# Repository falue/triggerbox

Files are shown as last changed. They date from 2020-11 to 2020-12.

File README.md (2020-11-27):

# triggerbox

## Introduction

This system allows for triggering up to six relays in a specific, as precice-as-possible rhythm.
It is designed for **high speed photography** or **high speed cinema shootings**,
where it can release water droplets, trigger explosions, activate a solenoid or anything that can be started with **up to 30VDC**.

Each relay can be tuned to start and stop being closed, starting when a button is pushed.
As in my hardware setup, each relay can hold up to **30VDC @ 5amps** and is able to trigger any external DC powered motor, electro magnet, or the like.

There is a 320x480 TFT display necessary to display a graphical menu, and give some feedback to the user. This can be omitted if you'd like to implement serial communication controls for user input.

The accuracy of the timing has to be determined. Theoretically you can set on / off timestamps in a microsecond fashion (0.000001s), but this is heavily influenced by the programs efficiency, the relay reaction time and the microcontrollers speed itself. More important than the preciseness to your entered timestamps though is the **repeatability**. If you do not change the hardware, the system should always trigger the relays with about the same lag, leading to the same results each time.

This system can be triggered with a regular hardwired push button. You are able to extend the triggering to another system: Connect it to your camera flash system, wire to two metal connectors, or use another arduino.

Maximum delay of any trigger is 35.79mins, theoretical minimum duration 0.000001s (1 microsecond, depending on the speed of the relays used).

## Hardware

This project needs eg. an Adafruit Metro M0 Express to work properly. Its program size and the demands for speed exceeds the capabilities of an Arduino UNO or Leonardo.

## Wiring diagram

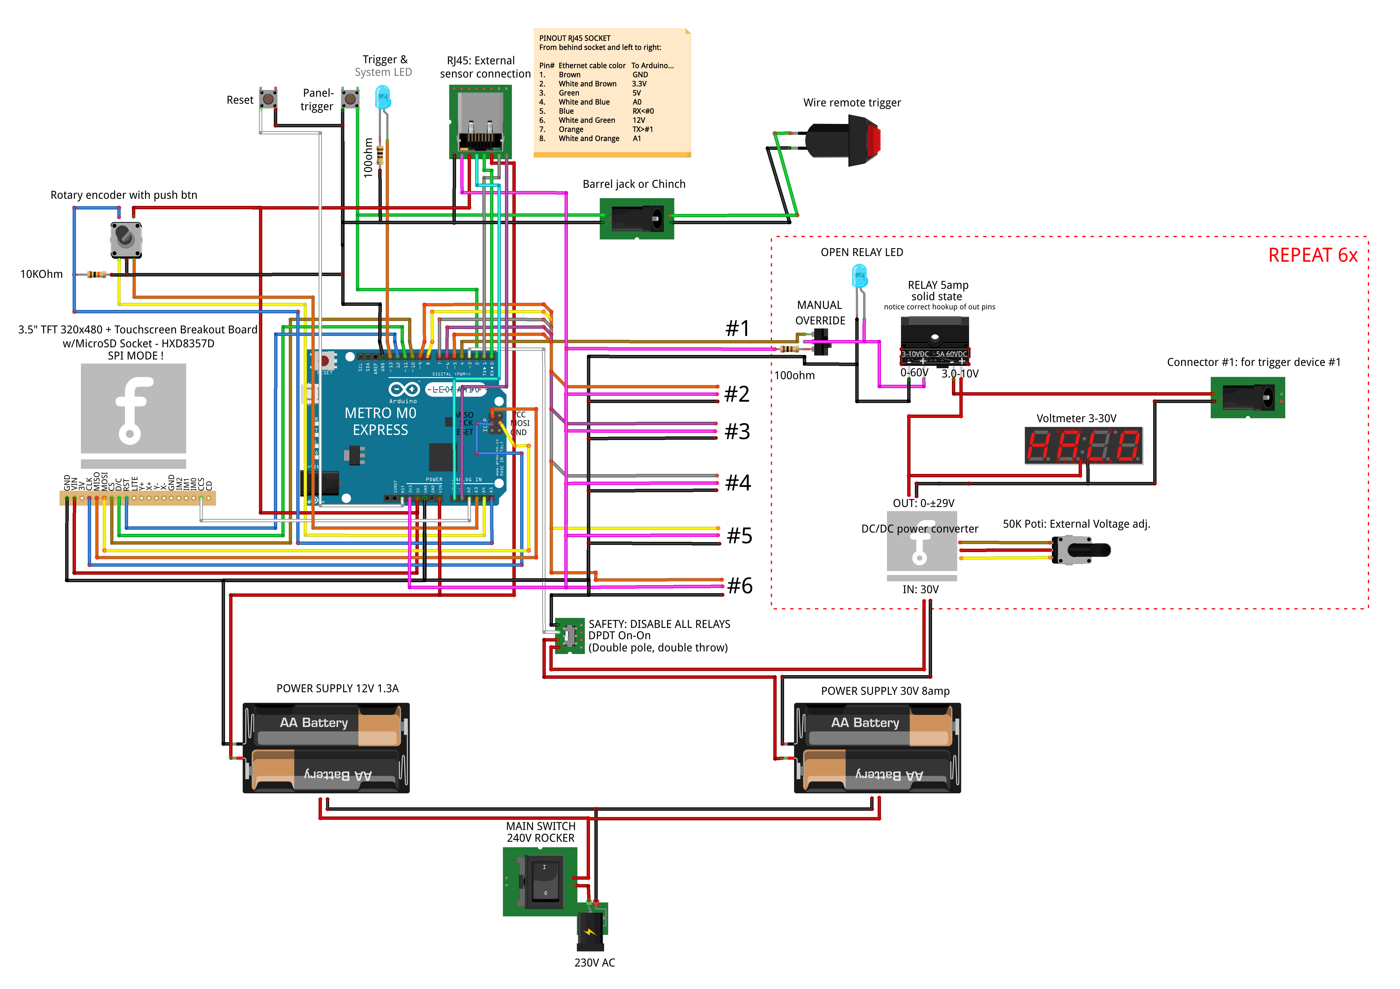
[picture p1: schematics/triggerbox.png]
wiring


### Hardware list

- Metro M0 Express - https://www.adafruit.com/product/3505
- TFT Touchscreen Breakout Board - HXD8357D - https://www.adafruit.com/product/2050
- 6pcs Solid state relays - https://www.digikey.ch/product-detail/en/sensata-crydom/CMX60D5/CC1667-ND/751911
- 30VDC power supply 8amp - https://www.components-store.com/product/MEAN-WELL/SP-240-30.html
- 5VDC power supply 5amp - https://www.components-store.com/product/MEAN-WELL/RS-25-5.html
- Generic rotary encoder
- Generic push button
- Some generic resistors
- Generic AC cold appliance socket

### Optional hardware
- 7pcs generic LEDs (display relay action)
- 6pcs DC/DC 15A Buck Adjustable 4-32V 12V to 1.2-32V 5V Converter Step Down Module DT (adjustment of relay voltage) - https://ebay.us/CVko1q
- 6pcs Generic 50KΩ potentiometer (allow for free placement of potentiometer of the Step Down Module)
- 6pcs LED Digital Voltmeter 0-100V (display chosen voltage) - https://de.aliexpress.com/item/33017235960.html?spm=a2g0s.9042311.0.0.64224c4dII9GZf

Keep an eye on the fact that your solid state relay can switch loads from ***0VDC*** to 30VDC.
Cheaper relays may only trigger loads from eg. ***14VDC*** to 30VDC, which may also work for your use case.

## Attention: Electricity

Although this setup allows for each relay to hold **5amps**, the sum of active loads in parallel **cannot be greater than 8 amps**.
The bottleneck is the 30VDC power supply with only 8amps. If you choose something beefier, you can trigger more loads @ 5amps in parallel.

Also, this system handles ***mains voltage***. No fingers where they do not belong. Its components are chosen based on a 230V AC/DC environment.

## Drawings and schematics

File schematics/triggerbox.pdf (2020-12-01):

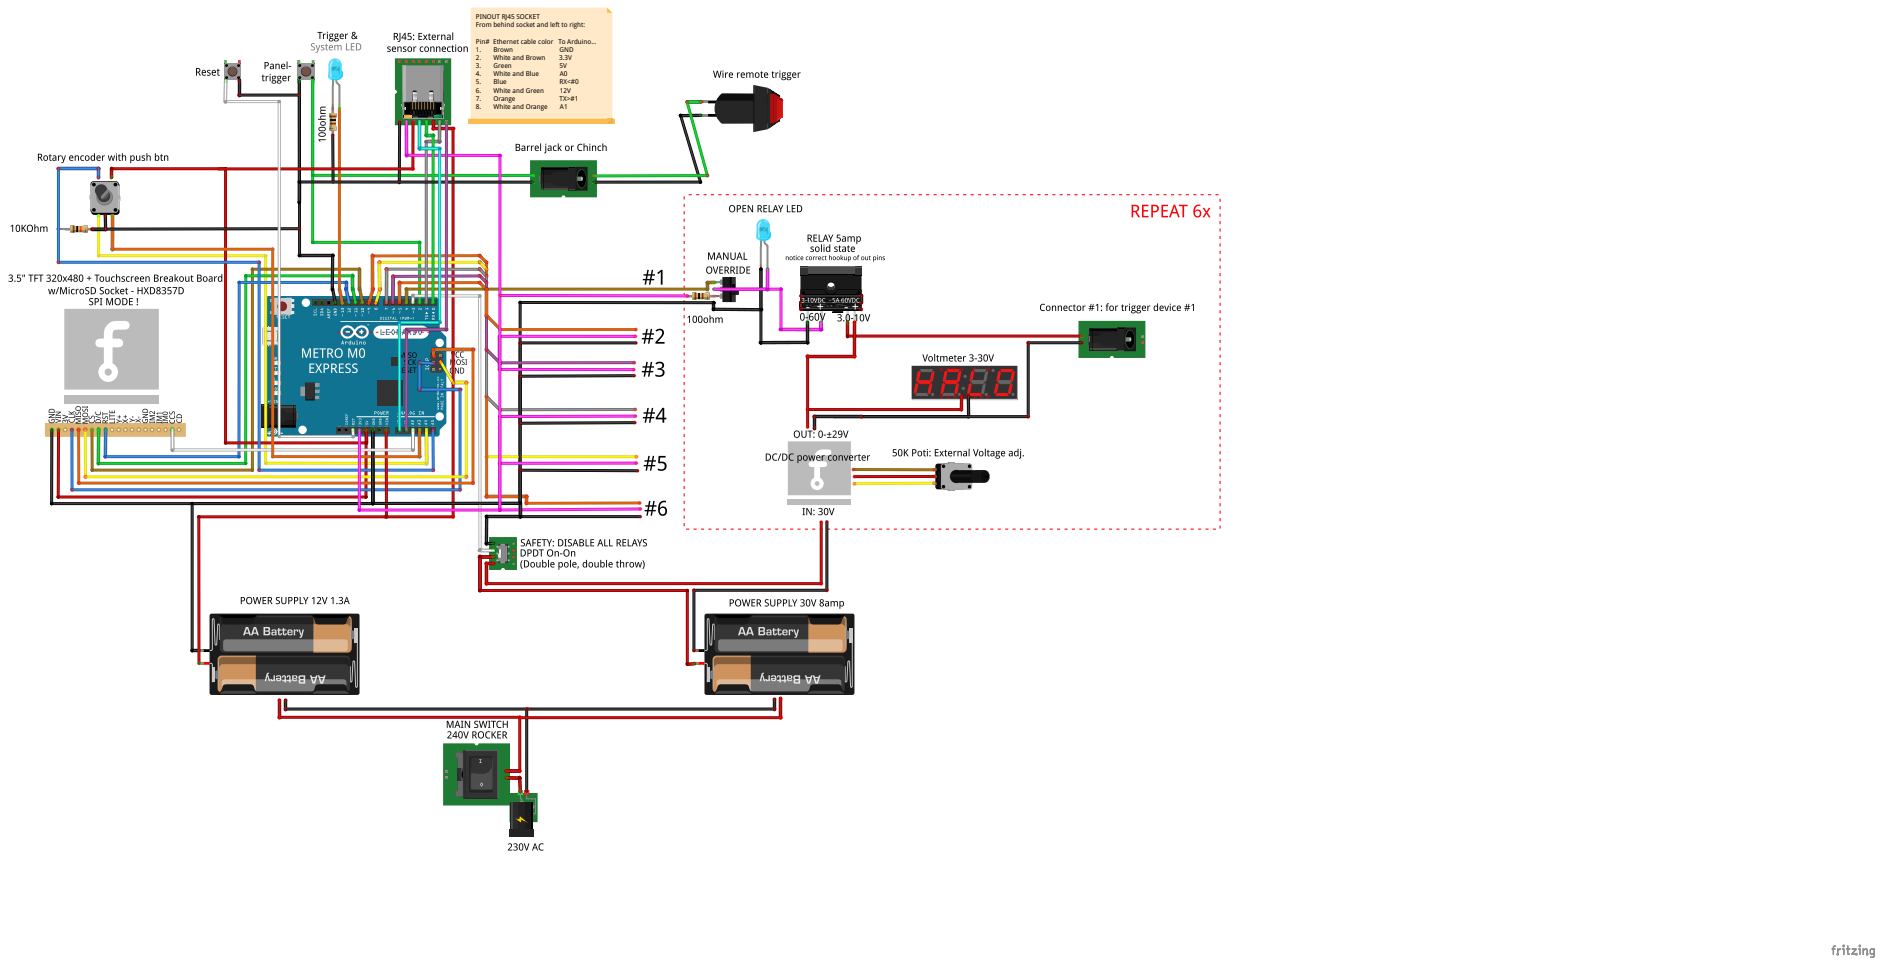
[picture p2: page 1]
Brown; GND; White and Brown; Green; White and Blue; Blue; White and Green; Orange; White and Orange

PINOUT RJ45 SOCKET
From behind socket and left to right:

Pin# Ethernet cable color To Arduino...

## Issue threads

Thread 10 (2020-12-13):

Pushing of Rotary Encoder lights up LEDs

falue, 2020-12-13:
If a relay is set to "manual override", during the push of the Rotary encoder btn, the LED lights up brigther.
Something to do with the 5V used for the push btn.
Maybe seperate the 5V GND and the 3.3V GND?

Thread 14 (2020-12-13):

Install more fuses

falue, 2020-12-13:
Maybe more fuses are needed to protect the expensive circuit? But where?
Some components are already protected by fuses, like the DC-DCconverter or the power supplies. But the relays and the TFT are not.

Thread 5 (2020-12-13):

Inverse trigger mechanics on demand

falue, 2020-12-13:
Allow any trigger relay to be set as "reverse", so that it is open on idle, but closed when triggering. Useful for eg. an electro magnet that should open for a specific moment.

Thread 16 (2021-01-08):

Make one relay trigger camera

falue, 2021-01-08:
One relay should be able to trigger the camera on a specific time.
i.e., wire bot poles of a relay to the external plug without a dimmer. replace "manual override" switch with a momentary switch to manually trigger camera.

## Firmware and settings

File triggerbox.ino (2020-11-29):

// INCLUDE LOCAL FILES -----------------------------------------------------------------------------
#include "includes.h"
#include "declarations.h"

// ACTIONS FOR INTERRUPTS --------------------------------------------------------------------------
// Push btn: Trigger
void triggerIsPushed() {
  if(millis() > lastTimeTriggered + 500) {
    #ifdef debug
      Serial.println("triggerIsPushed");
    #endif
    if(!editSettings && !safetyIsOn) {
      triggerIsActive = !triggerIsActive;
      if(!triggerIsActive) reset();
    } else {
      triggerIsActive = false;
      Serial.println("Safety first! Cannot trigger when in menu or when safety is on.");
    }
  }
  lastTimeTriggered = millis();
}

// Safety switch: two pole single throw
void safetySwitchChanged() {
  safetyIsOn = digitalRead(safetySwitchPin);
  if(safetyIsOn) {
    reset();
    drawSafetyPopUp();
    editSettings = false;  // exit menu when switch is thrown in edit mode
  } else {
    drawLayout();
  }
  // If, during rendering of TFT, switch was changed again, re-run function:
  if(digitalRead(safetySwitchPin) != safetyIsOn) safetySwitchChanged();
}

// SETUP --------------------------------------------------------------------------------------
void setup() {
  Serial.begin(115200);

  // Setup TFT
  tft.begin();
  tft.setRotation(1);
  screenWidth = tft.width();
  screenHeight = tft.height();

  // Draw Welcome screen
  splashScreen();

  delay(1500); // wait for serial monitor to catch up...
  Serial.println("TRIGGERBOX INITIALIZED");

  // Setup buttons
  pinMode(rotaryHomePin, INPUT);
  pinMode(triggerPin, INPUT_PULLUP);
  attachInterrupt(digitalPinToInterrupt(triggerPin), triggerIsPushed, RISING);
  pinMode(safetySwitchPin, INPUT_PULLUP);
  attachInterrupt(digitalPinToInterrupt(safetySwitchPin), safetySwitchChanged, CHANGE);

  // Setup rotary encoder
  rotaryEncoder.begin();

  // Set pinMode for relays
  for(int i = 0; i < numOfTriggers; i++) {
    /* Serial.print("triggers[i].pin: ");
    Serial.println(triggers[i].pin); */
    pinMode(triggers[i].pin, OUTPUT);
  }

  // TODO: Load "triggers" and settings (initDelay) from internal SPI Flash memory
  // https://learn.adafruit.com/adafruit-metro-m0-express-designed-for-circuitpython/using-spi-flash
  getDataFromMemory();

  // Initial save of settings
  calculateActions();
  printSettings();
  printActions();
  printTriggers();

  // Draw base layout
  drawLayout();

  safetyIsOn = digitalRead(safetySwitchPin);
  if(safetyIsOn) drawSafetyPopUp();
};


// LOOP ---------------------------------------------------------------------------------------
void loop() {
  editSettings = digitalRead(rotaryHomePin);
  if(editSettings && !safetyIsOn) {
    drawLock();
    drawFooter();  // redraw because buttons show up
    drawInitDelayButton();  // redraw because button is now selected
    Serial.println("---------");
    Serial.println("MENU");
    Serial.println("---------");
    Serial.println("Set initial delay..");
    delay(250); // wait for button to be released
  }

  // If rotary button is pressed and safety is not on, enter menu
  while(editSettings && !safetyIsOn) {
    menu();
    // If inside menu() "save" was selected, calculate actions
    if(!editSettings && !safetyIsOn) {
      calculateActions();
      printSettings();
      printActions();
      printTriggers();
      saveDataToMemory();
      drawLayout();
      Serial.println("Triggers and settings saved.");
    }
  }
  
  // If trigger push btn is pressed
  if(triggerIsActive) triggerAction();

  // Cut the loop() some slack
  delay(100);
};


// ACTIONS ------------------------------------------------------------------------------------
void menu() {
  // Names of menu items to display
  String menuDisplay[numOfMenuIds] = {
    F("Set initial delay.."),
    F("setRelay-00-startPoint"), F("setRelay-00-endPoint"), F("toggleRelay-00"),
    F("setRelay-01-startPoint"), F("setRelay-01-endPoint"), F("toggleRelay-01"),
    F("setRelay-02-startPoint"), F("setRelay-02-endPoint"), F("toggleRelay-02"),
    F("setRelay-03-startPoint"), F("setRelay-03-endPoint"), F("toggleRelay-03"),
    F("setRelay-04-startPoint"), F("setRelay-04-endPoint"), F("toggleRelay-04"),
    F("setRelay-05-startPoint"), F("setRelay-05-endPoint"), F("toggleRelay-05"),
    F("Set all to default"),
    F("Save and exit")
  };

  String selectedMenu = menuIds[menuSelector];
  String selectedMenuDisplay = menuDisplay[menuSelector];

  rotaryDirection = readRotaryEncoder(false);
  if(rotaryDirection != 0) {
    menuSelector += rotaryDirection;
    if(menuSelector > numOfMenuIds-1) menuSelector = 0;
    if(menuSelector < 0) menuSelector = numOfMenuIds-1;
    // menu level
    selectedMenu = menuIds[menuSelector];
    selectedMenuDisplay = menuDisplay[menuSelector];

    drawFooterButtons();  // redraw buttons to select or deselect
    drawInitDelayButton();  // redraw buttons to select or deselect

    // highlight relay parts
    if(selectedMenu.startsWith("setRelay") || selectedMenu.startsWith("toggleRelay")) {
      if(selectedMenu.startsWith("setRelay")) {
        relayIndex = selectedMenu.substring(9, 11).toInt();  // i know...
      } else {
        relayIndex = selectedMenu.substring(12, 14).toInt();  // i know...
      }
      if(relayIndex - 1 >= 0) drawTrigger(relayIndex-1);  // clear previous highlight
      drawTrigger(relayIndex);  // Draw to display
      if(relayIndex + 1 < numOfTriggers) drawTrigger(relayIndex+1);  // clear next highlight
      #ifdef debug
        Serial.println(getRelayMenuItem(relayIndex, selectedMenuDisplay));  
      #endif
    } else {
      #ifdef debug
        Serial.println(selectedMenuDisplay);
      #endif
    }

    if(selectedMenu == "initDelay") {  // redraw selection of trigger
      drawTrigger(0);
    }
    if(selectedMenu == "reset") {  // redraw selection of trigger
      drawTrigger(numOfTriggers-1);
    }
  }

  // Edit initDelay
  if(digitalRead(rotaryHomePin) && selectedMenu == "initDelay") {
    drawPopUp("Set initial delay");
    drawPopUpContent(timestampToFloatString(initDelay, "s", false), "");
    delay(250);  // wait for button to be depressed
    Serial.print("Edit initDelay:\t");
    Serial.println(initDelay);
    initDelay = setValueWithRotaryEncoder(initDelay, 0, 0, 1000, true);  // Edit [0.000]0000
    initDelay = setValueWithRotaryEncoder(initDelay, 0, 0, 1, true);  // Edit 0.000[0000]
    Serial.print("Saved initDelay:\t");
    Serial.print(initDelay);
    Serial.println("μs ("+String(initDelay / 1000000.0)+"..s)");
    drawLayout();
    delay(250);  // wait for btn release
  }

  // Edit start & end timestamps of relays
  if(digitalRead(rotaryHomePin) && selectedMenu.startsWith("setRelay")) {
    String relayTimepointToEdit = selectedMenu.substring(12);
    delay(250);  // wait for button to be depressed
    long lastTimeMoved = millis();

    if(relayTimepointToEdit == "startPoint") {
      drawPopUp("Set startpoint #" + String(relayIndex+1));
      drawPopUpContent(timestampToFloatString(triggers[relayIndex].startPoint, "s", false), "");
      Serial.println("Edit start point:");
      long initialGap = triggers[relayIndex].endPoint - triggers[relayIndex].startPoint;
      triggers[relayIndex].startPoint  = setValueWithRotaryEncoder(triggers[relayIndex].startPoint, 0, 2147483646-initialGap, 1000, true);  // Edit [0.000]0000
      triggers[relayIndex].startPoint  = setValueWithRotaryEncoder(triggers[relayIndex].startPoint, 0, 2147483646-initialGap, 1, true);  // Edit 0.000[0000]
      
      // re-set endpoint
      triggers[relayIndex].endPoint = triggers[relayIndex].startPoint + initialGap;
      Serial.print("Saved startPoint");
      Serial.print(triggers[relayIndex].startPoint);
      Serial.println("μs ("+String(triggers[relayIndex].startPoint / 1000000.0)+"..s)");

    } else {
      drawPopUp("Set duration #" + String(relayIndex+1));
      drawPopUpContent(timestampToFloatString(triggers[relayIndex].endPoint - triggers[relayIndex].startPoint, "s", false), "");
      Serial.println("Edit end point:");
      long delay = triggers[relayIndex].endPoint - triggers[relayIndex].startPoint;
      delay  = setValueWithRotaryEncoder(delay, 1, 0, 1000, true);  // Edit [0.000]0000
      delay  = setValueWithRotaryEncoder(delay, 1, 0, 1, true);  // Edit 0.000[0000]
      triggers[relayIndex].endPoint = triggers[relayIndex].startPoint + delay;
      Serial.print("Saved endPoint ");
      Serial.print(triggers[relayIndex].endPoint);
      Serial.println("μs ("+String(triggers[relayIndex].endPoint / 1000000.0)+"..s)");
    }
    drawLayout();
    delay(250);  // wait for btn release
  }

  if(digitalRead(rotaryHomePin) && selectedMenu.startsWith("toggleRelay")) {
    Serial.print("Edit active nr. ");
    Serial.print("di/enable ");
    Serial.println(relayIndex);
    triggers[relayIndex].active = !triggers[relayIndex].active;
    delay(250);  // wait for btn release
    editSettings = false;
  }

  // Reset to default
  if(digitalRead(rotaryHomePin) && selectedMenu == "reset") {
    initDelay = 0;
    triggers[0] = {4, 0, 1000000, true};
	  triggers[1] = {5, 1000000, 2000000, true};
	  triggers[2] = {6, 2000000, 3000000, true};
	  triggers[3] = {7, 3000000, 3500000, true};
	  triggers[4] = {8, 4000000, 4500000, true};
	  triggers[5] = {9, 5000000, 5600000, true};
    delay(250);  // wait for btn release
    editSettings = false;
  }

  // Exit menu
  if(digitalRead(rotaryHomePin) && (selectedMenu == "exit")) {
    Serial.println("Exit menu.");
    delay(250);  // wait for btn release
    editSettings = false;
  }
}

long setValueWithRotaryEncoder(long value, long min, long max, int multiplicator, boolean inertia) {
  long lastTimeMoved = millis();
  max = max == 0 ? 2147483646 : max;  // if 0 is max, use highest possible long
  while(!digitalRead(rotaryHomePin)) {
    long reading = readRotaryEncoder(inertia)*multiplicator;
    if(reading != 0) {
      value += reading;
      //value = value >= 0 ? value : 0;
      value = value >= min ? value : min;
      value = value <= max ? value : max;  // max size of type long (35.79min)
      /* Serial.print(value);
      Serial.println("μs ("+String(value / 1000000.0)+"..s)"); */
      lastTimeMoved = millis();
    }
    // to preserve inertia of rotary encoder, only safe this once in a while
    if(millis() - lastTimeMoved > 200 && lastTimeMoved != 0) {
      String valueAsText = timestampToFloatString(value, "s", false);
      String indicator = getEditMarker(valueAsText.length(), multiplicator == 1);
      drawPopUpContent(valueAsText, indicator);
      lastTimeMoved = 0;
    }
  }
  delay(250);  // wait for btn release
  return value;
}

long readRotaryEncoder(boolean inertia) {
  uint8_t reading = rotaryEncoder.read();
  if (reading) {
    int speed = rotaryEncoder.speed();
    int direction = reading == DIR_CW ? 1 : -1;
    long step = inertia ? (pow(10, int(speed/5))+.99) * direction : direction;  // speedramps! +.99 to round up int
    return step;
  } else {
    return 0;
  }
}

String getRelayMenuItem(int relayIndex, String nameOfMenu) {
  String relayTimepointToEdit = nameOfMenu.substring(12);
  if(relayTimepointToEdit == "startPoint"){
    return "Relay " + String(relayIndex+1) +
           " - Start:  T+" +String(triggers[relayIndex].startPoint / 1000000.0) + "s";
  } else {
    return "Relay " + String(relayIndex+1) + " - Duration: " +
           String((triggers[relayIndex].endPoint-triggers[relayIndex].startPoint) / 1000000.0) + "s" +
           " (T+"+String(triggers[relayIndex].endPoint / 1000000.0)+"s)";
  }
}

//action* calculateActions() {
void calculateActions() {
  // Reset actions struct array
  memset(actions, 0, maxActions);

  // set "actions" according to "triggers"
  Serial.println("Calculate actions..");
  // Serial.println("----------------\nbefore collections: ");
  //printTriggers();

  long actionTimestamps[maxActions];
  numOfActions = 0;

  // Collect all start- and endpoints
  for(int i = 0; i < numOfTriggers; i++) {
    if(triggers[i].active) {
      actionTimestamps[numOfActions] = triggers[i].startPoint;
      numOfActions++;
      actionTimestamps[numOfActions] = triggers[i].endPoint;
      numOfActions++;
    }
  }
  
  // proof
  // Print collected timestamps
  /* for(int i = 0; i < numOfActions; i++) {
    Serial.println(actionTimestamps[i]);
  }
  Serial.println("\n----------------\nSorted:"); */

  // sort "actionTimestamps" linear 0 > ...
  sortArray(actionTimestamps, numOfActions);

  // proof
  /* Serial.print("numOfActions: ");
  Serial.println(numOfActions);
  for(int i = 0; i < numOfActions; i++) {
    Serial.println(actionTimestamps[i]);
  } */

  // Overwrite doublicated elements
  long lastValue = -1;
  int newNumOfActions = numOfActions;
  for(int i = 0; i < numOfActions; i++) {
    if(actionTimestamps[i] == lastValue) {
      lastValue = actionTimestamps[i];
      actionTimestamps[i] = 2147483646;  // move to back of array
      newNumOfActions -= 1;
    } else {
      lastValue = actionTimestamps[i];  // Yes must be here.
    }
  }

  // Resort to remove doublicates
  sortArray(actionTimestamps, numOfActions);  
  numOfActions = newNumOfActions;

  // proof
  /* Serial.println("-------");
  Serial.print("numOfActions: ");
  Serial.println(numOfActions);
  for(int i = 0; i < numOfActions; i++) {
    Serial.println(actionTimestamps[i]);
  }
  Serial.println("-------"); */

  // iterate over "actionTimestamps"
  long lastTimestamp = 0;
  for(int i = 0; i < numOfActions; i++) {
    actions[i].timestamp = actionTimestamps[i]-lastTimestamp;  // Relative time from action to action
    //actions[i].pins = {};
    /* Serial.println();
    Serial.print("Fill trigger #");
    Serial.print(i);
    Serial.print("\tactionTimestamps: ");
    Serial.print(actionTimestamps[i]); */
    /* Serial.print("\tI: ");
    Serial.print(i);
    Serial.print("\tnumOfTriggers: ");
    Serial.println(numOfTriggers); */

    /* Serial.print("lastTimestamp:\t");
    Serial.print(lastTimestamp); */
    /* Serial.print("\tDelay:\t");
    Serial.println(actionTimestamps[i]-lastTimestamp); */

    int countOfTriggerActions = 0;  // 1;
    for(int x = 0; x < numOfTriggers; x++) {
      // add startPoints and endPoints
      if(
        triggers[x].active &&
        (triggers[x].startPoint == actionTimestamps[i] || triggers[x].endPoint == actionTimestamps[i])
        ) {
        /* Serial.print("\tAction #");
        Serial.print(countOfTriggerActions);
        Serial.print(",\tX: ");
        Serial.print(x);
        Serial.print("\t.startPoint: ");
        Serial.print(triggers[x].startPoint);
        Serial.print("\t.endPoint: ");
        Serial.print(triggers[x].endPoint);
        Serial.print("\t.pin: ");
        Serial.print(triggers[x].pin);
        Serial.print("\tOn/Off: ");
        Serial.println(triggers[x].startPoint == actionTimestamps[i]); */

        /* 
        typedef struct action {
        long timestamp;
        int triggerAction;  // number of triggerSetup* pins...
        triggerSetup* pins;
        
        typedef struct triggerSetup {
        int pin;
        long startPoint;
        long endPoint;
        boolean active;
        }data;
        }; */

        actions[i].pins[countOfTriggerActions] = {
          triggers[x].pin,
          triggers[x].startPoint,  // this is maybe not used in triggerActions()
          triggers[x].endPoint,  // this is maybe not used in triggerActions()
          triggers[x].startPoint == actionTimestamps[i],  // Set "active" to true or false
        };
        countOfTriggerActions += 1;
      }
    }
    actions[i].triggerAction = countOfTriggerActions;
    lastTimestamp = actionTimestamps[i];
  }
};


void printTriggers() {
  for(int i = 0; i < numOfTriggers; i++) {
    Serial.print("-------\nTrigger #");
    Serial.print(i);
    Serial.print("\t");
    Serial.print(triggers[i].pin);
    Serial.print("\t");
    Serial.print(triggers[i].startPoint);
    Serial.print("\t");
    Serial.print(triggers[i].endPoint);
    Serial.print("\t");
    Serial.println(triggers[i].active);
  }
}

void printActions() {
  Serial.println("Current Actions:");
  for(int i = 0; i < numOfActions; i++) {
    Serial.print("-------\nTrigger #");
    Serial.print(i);
    Serial.print("\tDelay: ");
    Serial.print(actions[i].timestamp);
    Serial.print("\ttriggerAction: ");
    Serial.println(actions[i].triggerAction);
    for(int x = 0; x < actions[i].triggerAction; x++) {
      Serial.print("  action #");
      Serial.print(x);
      Serial.print("\tpin: ");
      Serial.print(actions[i].pins[x].pin);
      /* Serial.print("\tstartPoint:");
      Serial.print(actions[i].pins[x].startPoint);
      Serial.print("\tendPoint:");
      Serial.print(actions[i].pins[x].endPoint); */
      Serial.print("\tOn/Off: ");
      Serial.println(actions[i].pins[x].active);
    }
  }
}

void printSettings() {
  Serial.println("---------");
  Serial.println("SETTINGS");
  Serial.println("---------");
  Serial.print("Initial delay:\t");
  Serial.print(initDelay);
  Serial.println("μs");
}

void triggerAction() {
  #ifdef debug
    Serial.println("Actions triggered");
  #endif
  digitalWrite(triggerLedPin, HIGH);
  // Wait at beginning and, if there is time, draw red dot on tft
  if(initDelay > 0) {
    if(initDelay > 4000 && !hasShownTriggerOnTft) {  // it takes ~3031ys to draw the red circle with white border
      wait(initDelay - drawTriggerAction(true));
    } else {
      wait(initDelay);
    }
  }

  for(int i = 0; i < numOfActions && triggerIsActive; i++) {
    #ifdef debug
      Serial.println("---------");
      Serial.print("Trigger #");
      Serial.print(i);
      Serial.println("..");
    #endif

    // If there is time, draw red dot on tft
    if(actions[i].timestamp > 4000 && !hasShownTriggerOnTft) {  // it takes ~3031ys to draw the red circle with white border
      wait(actions[i].timestamp - drawTriggerAction(true));
    } else {
      wait(actions[i].timestamp);
    }

    // If trigger was not aborted in the meantime...
    if(triggerIsActive) {
      // Do all the action now
      executeAction(actions[i].triggerAction, actions[i].pins);
    } else {
      // Trigger btn was pressed again to abort.
      // reset() happens when while loop in main loop() is exited.
      Serial.println("Abort senquence initiated prematurely.");
    }
  }
  // End of for loop reached
  if(triggerIsActive) {
    Serial.println("End of all actions reached.");
    reset();
  }
};

void executeAction(int triggerActions, triggerSetup* pins) {
  #ifdef debug
    Serial.print("\tNo. of actions: ");
    Serial.println(triggerActions);
  #endif

  for(int i = 0; i < triggerActions; i++) {
    #ifdef debug
      Serial.print("\tPin: ");
      Serial.print(pins[i].pin);
      Serial.print(", startPoint: ");
      Serial.print(pins[i].startPoint);
      Serial.print(", endPoint: ");
      Serial.print(pins[i].endPoint);
      Serial.print(", active: ");
      Serial.println(pins[i].active);
    #endif

    // Set the relay according to specs:
    digitalWrite(pins[i].pin, pins[i].active);
  }
}

// Reset all relays to LOW
void reset() {
  triggerIsActive = false;
  // Set every pin to LOW
  Serial.println("reset.");
  for(int i = 0; i < numOfTriggers; i++) {
    digitalWrite(triggers[i].pin, LOW);
  }
  digitalWrite(triggerLedPin, LOW);
  drawTriggerAction(false);
};

// Save triggers and settings (initDelay) to spi-flash
void saveDataToMemory() {
  // https://learn.adafruit.com/adafruit-metro-m0-express-designed-for-circuitpython/using-spi-flash

  // Save "initDelay" to memory
  // EEPROM.writeLong(EEPROMaddressLong,initDelay);

  // Save "triggers" to memory
  /* for(int i = 0; i < numOfTriggers; i++) {
    EEPROM.writeInt(EEPROMaddressInt, triggers[i].pin);
    EEPROM.writeLong(EEPROMaddressLong, triggers[i].startPoint);
    EEPROM.writeLong(EEPROMaddressLong, triggers[i].endPoint);
    EEPROM.writeInt(EEPROMaddressInt, triggers[i].active);
  } */
}

// Get triggers and settings (initDelay) from spi-flash
void getDataFromMemory() {
  // https://learn.adafruit.com/adafruit-metro-m0-express-designed-for-circuitpython/using-spi-flash

  // Get "initDelay" from memory
  // initDelay = EEPROM.readLong(EEPROMaddressLong);

  // Get "triggers" from memory
  /* for(int i = 0; i < numOfTriggers; i++) {
    triggers[i].pin = EEPROM.readInt(EEPROMaddressInt);
    triggers[i].startPoint = EEPROM.readLong(EEPROMaddressLong);
    triggers[i].endPoint = EEPROM.readLong(EEPROMaddressLong);
    triggers[i].active = EEPROM.readInt(EEPROMaddressInt);
  } */
}

void wait(long delayTime) {
  long stop = micros() + delayTime;
  while(micros() <= stop && triggerIsActive) {
    // twiddle your thumbs
  }
}

String timestampToFloatString(long timestamp, String append, boolean shorten) {
  // Max lenght of long timestamp: 2147483646 / 10 digits
  int padding = timestamp > 99999999 ? 10 : 9;  // If large number, increase leading spaces
  char result[padding];  // 123.1234567
  dtostrf(timestamp/1000000.0, padding, 6, result); 
  // If large number, do not append "s" to save space
  return timestamp > 99999999 && shorten
    ? result
    : result + append;
}

// Should be in standard arduino library?
char *dtostrf (double val, signed char width, unsigned char prec, char *sout) {
  asm(".global _printf_float");
  char fmt[20];
  sprintf(fmt, "%%%d.%df", width, prec);
  sprintf(sout, fmt, val);
  return sout;
}


// TFT ----------------------------------------------------------------------------
// Center text in between a rectangle x & y
void centerText(const String &text, int x, int y) {
  int16_t x1, y1;
  uint16_t w, h;
  tft.getTextBounds(text, x, y, &x1, &y1, &w, &h); //calc width of new string
  tft.setCursor(x - w / 2, y);
  tft.print(text);
}
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

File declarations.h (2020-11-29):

// PIN DECLARATION ----------------------------------------------------------------------------
const int triggerPin = 2;
volatile const int safetySwitchPin = 3;
const int triggerLedPin = 13;
const int rotaryHomePin = A5;
MD_REncoder rotaryEncoder = MD_REncoder(A4, A3);
#define TFT_CS 10
#define TFT_DC 11
#define TFT_RST 12

// VARS ---------------------------------------------------------------------------------------
volatile boolean triggerIsActive = false;
boolean hasShownTriggerOnTft = false;
volatile boolean safetyIsOn = false;
long initDelay = 0;  // MICROSECONDS eg. 1000000 (= 1s)
volatile long lastTimeTriggered = 0;
long rotaryOldPosition = 0;
long rotaryCurrentDirection = 0;
int rotaryDirection = 0;
volatile boolean editSettings = false;
int menuSelector = 0;

// Menu system
int relayIndex = 0;
const int numOfMenuIds = 21;
String menuIds[numOfMenuIds] = {
  F("initDelay"),
  F("setRelay-00-startPoint"), F("setRelay-00-endPoint"), F("toggleRelay-00"),
  F("setRelay-01-startPoint"), F("setRelay-01-endPoint"), F("toggleRelay-01"),
  F("setRelay-02-startPoint"), F("setRelay-02-endPoint"), F("toggleRelay-02"),
  F("setRelay-03-startPoint"), F("setRelay-03-endPoint"), F("toggleRelay-03"),
  F("setRelay-04-startPoint"), F("setRelay-04-endPoint"), F("toggleRelay-04"),
  F("setRelay-05-startPoint"), F("setRelay-05-endPoint"), F("toggleRelay-05"),
  F("reset"),
  F("exit")
};
int marginTopTriggerlist = 87;  // from top of display to table of triggers

// DEFINE -------------------------------------------------------------------------------------
#define debug  // More Serial.print statements everywhere

// define struct type data
typedef struct triggerSetup {
  int pin;
  long startPoint;
  long endPoint;
  boolean active;
};

const int numOfTriggers = 6;  // max physical connections
// TIMESTAMPS IN MICROSECONDS.
triggerSetup triggers[numOfTriggers] = {
  {4, 0, 1000000, true},
	{5, 100000, 100009, true},
	{6, 2000000, 2000009, true},
	{7, 30000000, 30900000, true},
	{8, 400000000, 400000009, true},
	{9, 2147483640, 2147483645, true},
};

typedef struct action {
  long timestamp;
  int triggerAction;  // number of triggerSetup pins...
  triggerSetup pins[numOfTriggers];  // "pins[numOfTriggers]" USES LOTS OF MEMORY
};

// max possibilities of actions - each trigger an unique start/end timestamp
const int maxActions = numOfTriggers*2;
action actions[maxActions];
int numOfActions = 0;

// TFT
// Use hardware SPI (on Uno, #13, #12, #11) and the above for CS/DC
Adafruit_HX8357 tft = Adafruit_HX8357(TFT_CS, TFT_DC, TFT_RST);
int screenWidth = 0;
int screenHeight = 0;

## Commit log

2020-11-24 add 'trigger state' LED
2020-11-24 add 'remove EEPROM library, set up to use SPI flash memory instead
2020-11-25 Add TFT schematic
    [triggerbox.fzz]
2020-11-25 Use TFT; use safety switch, sovle everything
2020-11-25 bugfix title popup, again
    [triggerbox.ino]
2020-11-25 Update schematics
    [triggerbox.fzz]
2020-11-25 Update README with schematics
    [triggerbox.fzz]
2020-11-25 format timestamps on TFT
    [triggerbox.fzz]
2020-11-25 faster rotary encoder speedramp
2020-11-25 less serial.prints if not debug
2020-11-25 more detailed schematics
    [triggerbox.fzz]
2020-11-26 Rename footer button to "defaults"
2020-11-27 Move rotary pins to A2/A3, update wiring diagram
    [triggerbox.fzz]
2020-11-27 Reset() & exit menu when throwing safety
    [triggerbox.ino]
2020-11-29 Use 12V power supply, manual override from 3.3v pinwq
    [triggerbox.fzz]
2020-11-30 RJ45 wiring changed
    [triggerbox.fzz]
2020-12-01 Add resistors to override&trigger LED; add reset btn
    [triggerbox.fzz]
2020-12-01 Reverse polarity of OUT pins @ relay
    [triggerbox.fzz]
